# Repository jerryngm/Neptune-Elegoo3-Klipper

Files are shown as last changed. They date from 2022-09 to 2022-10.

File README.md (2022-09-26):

# Klipper Config File for Elegoo Neptune 3 (WIP)
Base Klipper Config file for Klipper. **Use at your own risk!!** Please read the comments in the file, you will need to calibrate your hotend heater PID and E-steps   
## 📄 **Todo:**  
 ✔️ X Y Z E Steppers config  
 ✔️ Heaters and Fans  
 ⭕ (WIP) ABL using Z- (ZNP Glevel board - Strain Gauge Sensor) - 8bit AVR (STM8S003F3P6) + HX711 (Load cell amplifier), this board send out z-end digital signal at predetermined weight, triggered by probe contact  
 ⭕ (WIP) Filament sensor  
 ⭕ (WIP) Klipper's Pressure Adance calibrate  
 ✔️ Klipper's Input Sharper. Mounts available, see below

## **👨‍🏫 Building Klipper Firmware**  
 **I have pre-complied the firmware, you can download "ZNP_ROBIN_NANO_Klipper.bin" then remove _Klipper from the name and copy this file to your SD Card**  
 If you would like to compile your own, please follow the instructions below:  
 Use the following config in make menuconfig    
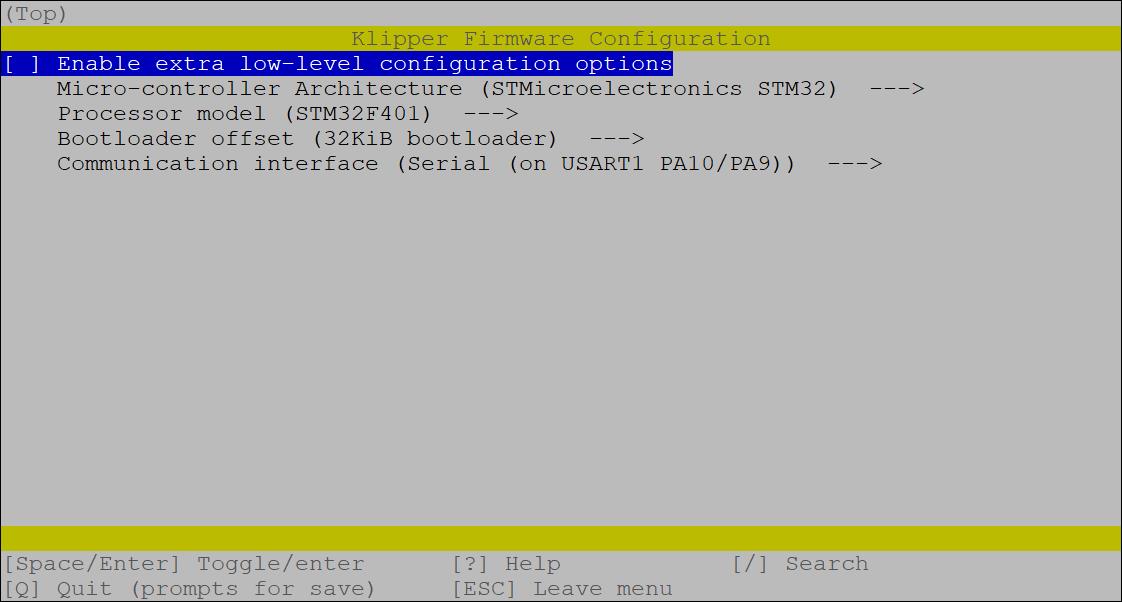
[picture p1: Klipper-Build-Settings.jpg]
  

Once compiled, copy klipper.bin to an SD card (root folder) then rename it to ZNP_ROBIN_NANO.bin, insert it to your Neptune then switch on.  
You can revert back to original firmware by placing the original firmware bin file to the SD card  

**I have also pre-complied the firmware, you can download "ZNP_ROBIN_NANO_Klipper.bin" then remove _Klipper from the name and copy this file to your SD Card**
 
 ## **🔧 Calibrations**  
 You will need to run your own PID calibration for the extruder heater, following the instructions here: https://www.klipper3d.org/Config_checks.html#calibrate-pid-settings or enter PID_CALIBRATE HEATER=extruder TARGET=170 into the console  
 Also extruder rotation_distance (I.e E-Steps): https://www.klipper3d.org/Rotation_Distance.html#calibrating-rotation_distance-on-extruders
 
 ## **🧭 Input Sharper - ADXL345 Mount**
 - [X Axis - Mount to X Carriage](https://github.com/jerryngm/Neptune-Elegoo3-Klipper/blob/main/Neptune3-ADXL345-HOTEND-X-Axis.stl)
 - [Y Axis - Mount to Bed](https://github.com/jerryngm/Neptune-Elegoo3-Klipper/blob/main/Neptune3-ADXL345-BED.stl)
 - -[Clamp to hold board in place for Bed mount, sandwich the board in the middle](https://github.com/jerryngm/Neptune-Elegoo3-Klipper/blob/main/Neptune3-ADXL345-BED-Clamp.stl)
 - [Fusion 360 source file, it's a mess tho but I included it here if you like to make any changes](https://github.com/jerryngm/Neptune-Elegoo3-Klipper/blob/main/Neptune%203%20-%20ADXL345%20-%20Mount%20v1.f3d)
- Print at 0.2 layer height
- Reuse screws from the screen case

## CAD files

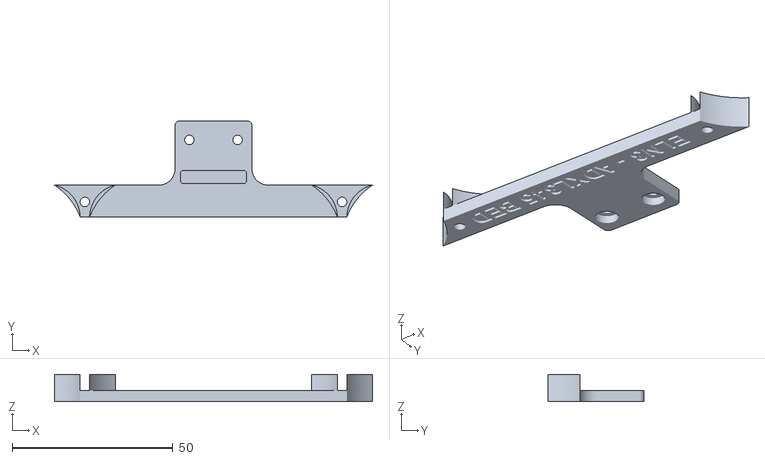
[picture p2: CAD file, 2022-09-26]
Neptune3-ADXL345-BED.stl
99.0 x 30.0 x 8.50

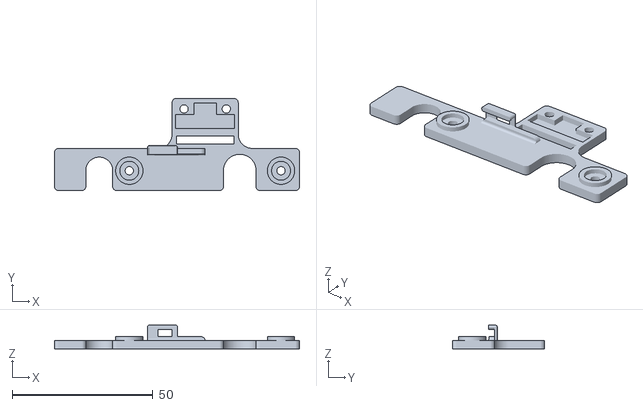
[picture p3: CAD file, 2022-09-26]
Neptune3-ADXL345-HOTEND-X-Axis.stl
87.0 x 32.8 x 8.48

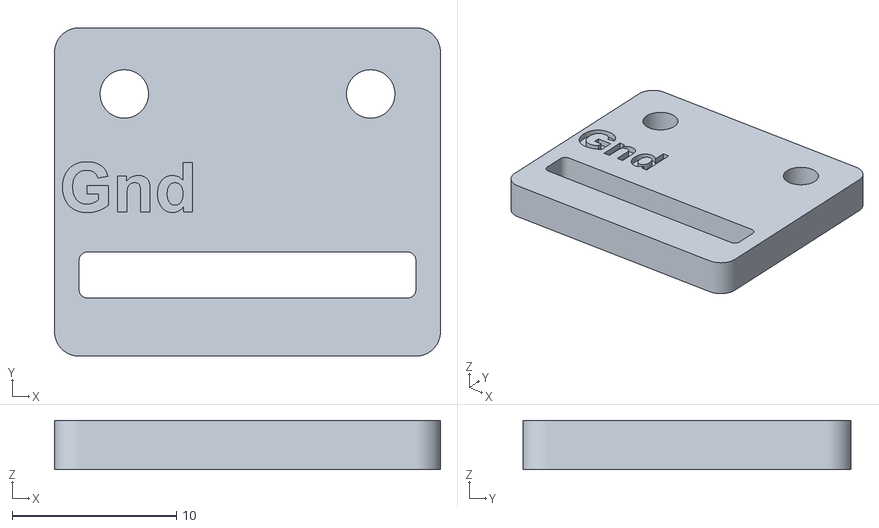
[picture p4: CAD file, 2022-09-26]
Neptune3-ADXL345-BED-Clamp.stl
23.5 x 20.0 x 3.00

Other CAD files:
Neptune 3 - ADXL345 - Mount v1.f3d

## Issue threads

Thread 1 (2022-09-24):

Contact

Fragmon, 2022-09-24:
Hello. We create the klipper firmware for the anycubic vyper. He has a strain gauge too. How can we contact you? We would help.

jerryngm, 2022-09-24:
If the printer used a dedicated board to connect to the Z- Endstop then you can enter that pin to your config file as probe or virtual Z end

Fragmon, 2022-09-24:
Do you have a pinout for the chip or the source for the Marlin? I only found for the neptune 2. And i wont messure all traces.

Gesendet von Mail<https://go.microsoft.com/fwlink/?LinkId=550986> für Windows

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

jerryngm, 2022-09-24:
If the manufacturer published the source code for Marlin then you can find it in the Pins src file, otherwise you can try your luck by looking up the board name, they tend to clone from other manufacturers.

Fragmon, 2022-09-24:
Anycubic open the marlin source for the vyper and i need that for the neptune because i need a few pins.

jerryngm, 2022-09-24:
You can find source code for Neptune 3 here
https://github.com/NARUTOfzr/Neptune_3

Fragmon, 2022-09-24:
I am blind thank you :-D

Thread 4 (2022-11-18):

Blank Display

nathantheone94, 2022-11-18:
HI Jerry,

I am aware that klipper will usually render the screen on the printer useless however i did notice that you have some firmware (DWIN_SET)

Currently this shows a blank grey screen, is there any further config required in order to utilise the neptune 3 touch screen?

DennAgain, 2024-04-03:
any update on this? i would love to utilize klipper but dont wanna render the touch screen useless

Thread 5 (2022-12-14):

Could I use this with the Neptune 3 Pro?

kozross, 2022-12-14:
How much would need to change to use this with the Neptune 3 Pro?

mygrexit, 2023-01-08:
Greet question, would be interested as well!

kozross, 2023-01-08:
Doesn't matter, I [already fixed this problem myself](https://github.com/Klipper3d/klipper/pull/5965).

mygrexit, 2023-01-08:
@kozross, was going to link it to you a few minutes ago until I realized that it's your PR. Thanks mate, much appreciated!

Closed 2023-01-08.

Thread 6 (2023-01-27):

Homing in the wrong direction

kLuTT44, 2023-01-27:
The homing works pretty well, but if I save a calibrated bed mesh into the printer.cfg, it moves upwards instead of down whenever I try to home it..

Closed 2023-02-12.

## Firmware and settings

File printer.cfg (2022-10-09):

# For the ZNP Robin Nano DW v2.1 board:
#   - Compile with the processor model STM32F401.
#   - Select the 32KiB bootloader,
#   - Select (Serial (on # USART1 PA10/PA9) for the communication interface.
# Note that the "make flash" command does not work with ZNP Robin boards. After
# running "make", run the following command:
# cp out/klipper.bin out/ZNP_ROBIN_NANO.bin
#
# Copy the file out/ZNP_ROBIN_NANO.bin to an SD card and then restart the printer with
# that SD card.
# See docs/Config_Reference.md for a description of parameters.

[mcu]
serial: /dev/serial/by-id/usb-1a86_USB_Serial-if00-port0
restart_method: command

[printer]
kinematics: cartesian
max_velocity: 300
max_accel: 3000
max_z_velocity: 5
max_z_accel: 100

[duplicate_pin_override]
pins: PC7, PC8, PC9, PC14 #Reuse Z-Stepper pins to drive the stepper manually and Z-Max Sensor pin

[stepper_x]
step_pin: !PC12
dir_pin: PB3
enable_pin: !PD2
microsteps: 16
rotation_distance: 40
endstop_pin: PA13
position_endstop: 0
position_max: 235
homing_speed: 50

[stepper_y]
step_pin: PC11
dir_pin: PA15
enable_pin: !PC10
microsteps: 16
rotation_distance: 40
endstop_pin: PB8
position_endstop: 0
position_max: 235
homing_speed: 50

[stepper_z]
step_pin: PC7
dir_pin: !PC9
enable_pin: !PC8
rotation_distance: 8
microsteps: 16
endstop_pin: probe:z_virtual_endstop # Use Z- as endstop
#Alternative homing config is available at @bsas fork https://github.com/bsas/Neptune-Elegoo3-Klipper
position_min: -1
position_max: 285
homing_speed: 0.1
second_homing_speed: 0.1
homing_retract_dist: 1.0

#Redefine Z-stepper so it can be driven independently using Klipper's Manual Stepper Gcode and Z-Max sensor can be used to stop the movement
[manual_stepper z-max]
step_pin: PC7
dir_pin: !PC9
enable_pin: !PC8
rotation_distance: 8
microsteps: 16
endstop_pin: !PC14

#Workaround to get the status of Z-Max optical sensor
[filament_switch_sensor z-max]
pause_on_runout: False
switch_pin: !PC14 

[homing_override]
axes: xyz
set_position_z: 0 #Temporary set Z as 0 so X and Y can be moved after XY homing
gcode:
 {% if printer["filament_switch_sensor z-max"].filament_detected == True %} #If Z-Max sensor is triggered, move Z up to advoid scratching Bed 
 MANUAL_STEPPER STEPPER=z-max SET_POSITION=0 SPEED=10 MOVE=5 STOP_ON_ENDSTOP=0 SYNC=0 #Move Z-Stepper using [manual_stepper] Gcode
 MANUAL_STEPPER STEPPER=z-max ENABLE=0
 G28 X0 Y0 #Home XY
 G0 X110 Y110 F5000 #Move XY to the middle
 G28 Z0 #Home Z
 G0 Z10 F100 #Move Z Up
 {% else %}
 #As above
 G28 X0 Y0
 G0 X110 Y110 F5000
 #At speed of 250mm/s, this movement will take ~12 seconds regardless of Z-Max Sensor status. (E.g. When sensor is triggered, Z will stop, however it will wait till the code is complete which is ~12s)
 #The movement is quite loud at this speed, you can reduce the speed thus increase waiting time. 
 MANUAL_STEPPER STEPPER=z-max ENABLE=1 SET_POSITION=285 SPEED=25 MOVE=0 STOP_ON_ENDSTOP=1 SYNC=0 
 MANUAL_STEPPER STEPPER=z-max ENABLE=0
 G28 Z0
 G0 Z10 F100
 {% endif %}

[extruder]
max_extrude_only_distance: 100.0
step_pin: PB10
dir_pin: PB1
enable_pin: !PC6
microsteps: 16
rotation_distance: 24 # Calibrate E-Steps https://www.klipper3d.org/Rotation_Distance.html#calibrating-rotation_distance-on-extruders
nozzle_diameter: 0.400
filament_diameter: 1.750
heater_pin: PA6
sensor_type: EPCOS 100K B57560G104F
sensor_pin: PC1
# Calibrate PID: https://www.klipper3d.org/Config_checks.html#calibrate-pid-settings
control: pid
pid_kp = 28.631
pid_ki = 1.853
pid_kd = 110.589
min_temp: 0
max_temp: 250

[heater_bed]
heater_pin: PA5
sensor_type: EPCOS 100K B57560G104F
sensor_pin: PC0
max_temp: 110
min_temp: 0
control: watermark

[heater_fan hotend_fan]
pin: PA7
heater: extruder
heater_temp: 50.0

[fan]
pin: PB0

[force_move]
enable_force_move: True

# Safe Z Home doesn't work with homing overide, the config below are implemented in homing_overide section
#[safe_z_home]
#home_xy_position: 110,110
#z_hop: 10

[probe]
pin: !PC13 # Use Z- as endstop
speed: 0.1
lift_speed: 0.5
samples_tolerance: 0.09
samples_tolerance_retries: 2
samples: 4
samples_result: median
z_offset = 0
activate_gcode:
	TARE_PROBE

[gcode_macro TARE_PROBE]
gcode:
	{action_respond_info("Wait")}
    G4 P1000
	{action_respond_info("Start")}

[bed_mesh]
speed: 20
horizontal_move_z: 1
algorithm: bicubic
mesh_min: 20,20
mesh_max: 200,200
probe_count: 4,4
fade_start: 1
fade_end: 50
fade_target: 0
#relative_reference_index: 6
#mesh_pps: 1
bicubic_tension: 0.15

[filament_motion_sensor filament_sensor]
extruder: extruder
pause_on_runout: true
switch_pin: PB4

#Input Sharper Setup
#[mcu rpi]
#serial: /tmp/klipper_host_mcu

#[adxl345]
#cs_pin: rpi:None

#[resonance_tester]
#accel_chip: adxl345
#probe_points:
    110, 110, 20  # an example

#[input_shaper]
#shaper_freq_x: 
#shaper_type_x: 
#shaper_freq_y: 
#shaper_type_y: 

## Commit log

2022-09-26 ADXL345 Mount
    [Neptune 3 - ADXL345 - Mount v1.f3d, Neptune3-ADXL345-BED-Clamp.stl, Neptune3-ADXL345-BED.stl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]
2022-10-06 Add filament sensor config
    [printer.cfg]
2022-10-06 Add information on alternative method of homing
    [printer.cfg]
2022-10-09 Faster Z Homing by ultilising Z-max opitcal sensor
    [printer.cfg]
2022-10-09 Fine tune homing movement
    [printer.cfg]
